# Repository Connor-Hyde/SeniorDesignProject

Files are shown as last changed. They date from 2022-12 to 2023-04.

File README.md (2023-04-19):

# Terra Table
# Table of Contents

1. [Project Description](#project-description)
2. [User Interface Specification](#user-interface-specification)
3. [Test Plan and Results](#test-plan-and-results)
4. [User Manual](#user-manual)
5. [Spring Final PPT Presentation](#spring-final-ppt-presentation)
6. [Final Expo Poster](#final-expo-poster)
7. [Assessments](#assessments)
    1. [Initial Self-Assessments](#initial-self-assessments)
    2. [Final Self-Assessments](#final-self-assessments)
8. [Summary of Hours and Justification](#summary-of-hours-and-justification)
9. [Summary of Expenses](#summary-of-expenses)
10. [Appendix](#appendix)

## Project Description

### Background
The purpose of this project is to elevate the gameplay experience of table-top role-playing games such as “Dungeons and Dragons”. These games are often played in the ‘theater of the mind’ using minimal props for visualizing the world in which the players are role-playing. However, many players do like to use a ‘battle mat’ to help visualize the specific locations and layouts of a certain area in the game.

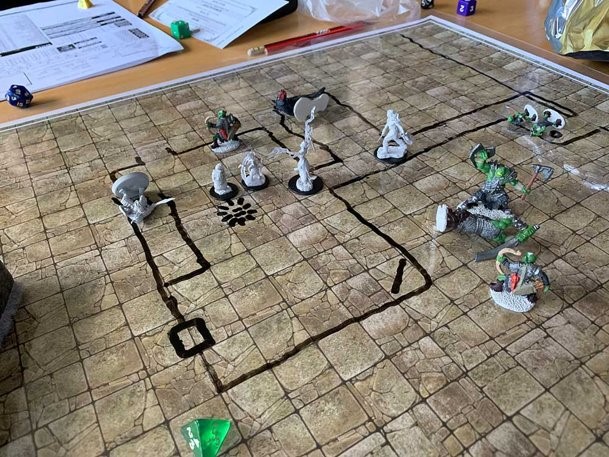
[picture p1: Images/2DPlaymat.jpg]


These mats consist of a large grid of squares. Each square represents a scaled down distance in game; players can use miniature figures of their characters to represent where they are in the world. The downside to these mats is that they are low tech and only two dimensional. Some players turn to using small blocks or walls to create a more 3D feeling to their environments, while others invest time and money into creating elaborate dioramas for their games.

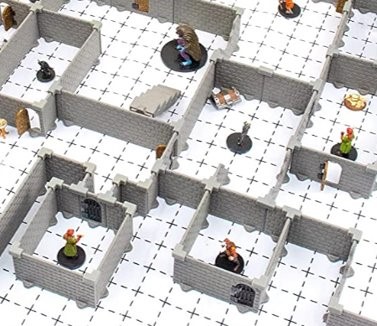
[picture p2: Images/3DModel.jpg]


This project aims to bridge the gap between low tech battle mats and high detail dioramas with programable, 3D topography, built into the game table.

### Objectives
This project aims to create a device that can be inserted into any table and convert it into a 3D topographical map that is fully programable to create scenes and landscapes for their gameplay. The final product will consist of a grid of cubes, each capable of being raised and lowered to create a 3D landscape. The shape of the scene will be determined by a graphical user interface where the players can create their map in 2D in the program and then watch as their creation comes to life in the table.

## User Interface Specification

The user interface was designed using Windows Presentation Foundation (WPF), and consists of 3 key features:

1. A slider for specifying height
2. 3 buttons, for executing actions
3. A 10x10 grid of squares, visually representing what the physical table will look like

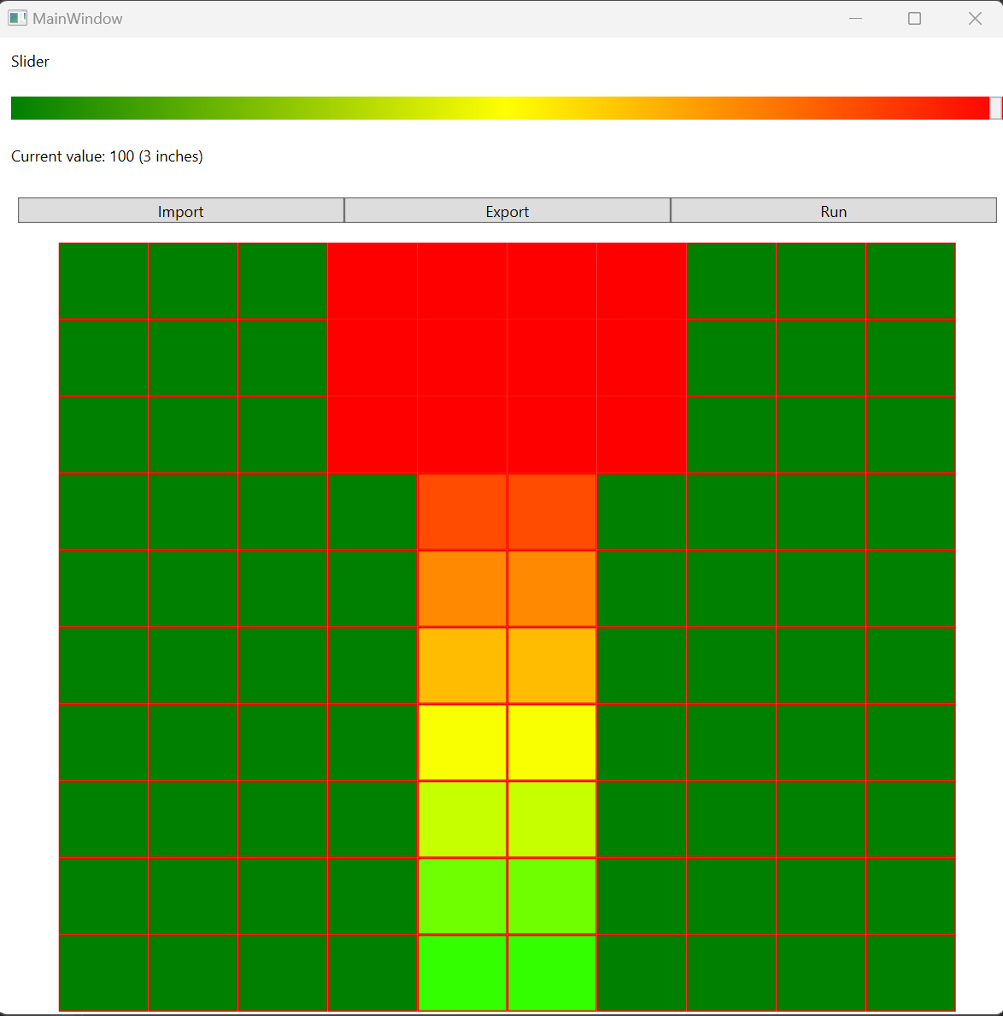
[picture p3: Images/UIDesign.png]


### Slider
The slider uses a gradient of colors from green to yellow to red, with a text box displaying the percentage of max height, and the corresponding height in inches. Whatever value is chosen on the slider will be applied to a grid square on click.

### Buttons
There are presently 3 buttons that allow the user to execute their respective actions:

1. Import: A text file can be imported, which will instantly apply a pre-recorded configuration to the grid.
2. Export: This exports the current configuration, so that at a later time it can be re-applied if desired.
3. Run: This executes the main functions of the table, sending the current configuration to the Arduino sketch. This is done by serialized communication with the board, and upon selecting this command the user will begin to see movements in the table until all cubes have been raised to desired height.

### Grid
The grid uses a gradient color scale to help the user visualize what they are creating on the table in 3 dimensions. From the image above, this would create something similar to a staircase, with a platform at the top. The idea was derived from topographical terrain maps that use gradients to visualize elevation on a 2 dimensional plane.

## Test Plan and Results

### Test Plan

For this project, the primary testing approach will be unit testing, supplemented by integration testing for more complex components. The goal is to adhere to Test-Driven Development (TDD) practices as closely as possible, as this has become a habit in professional work environments. Although TDD can sometimes be tedious, it is crucial to ensure that methods and classes are thoroughly tested.

Regardless of the specific approach, the project will have as many components (methods and classes) tested as feasible. Integration tests may be required when developing the Arduino aspect of the project, which might necessitate exploring various test suites capable of running both code segments concurrently in a single test.

For unit testing, NCrunch, a valuable tool for debugging and viewing all tests within a given solution simultaneously, will be utilized. Mocking frameworks and NUnit will be employed to construct the tests.

### Test Results

All tests can be found in the /Code/TerrainTableWpf/Tests subdirectory. There were 10 tests in total to ensure that all logic is set up properly, the testing matrix summarizing all aspects of the testing can be found below:

| Test Identifier | Purpose of Test | Inputs for Test | Expected Outputs/Results | Unit Test Indication |
| --- | --- | --- | --- | --- |
| MainWindowConstructor_CreatesExpectedTerrainGrid | Tests that the construction of the UI grid sets the initial state properly | None | Expected that all squares have an initial 'Green' state | Pass |
| ReadFileContent_ReturnsCorrectFileContent | Ensures the file reader returns exactly what is in the text files for importing | Encoded string of file content | Should return string decoded | Pass |
| DeserializeAndSetTerrainGrid_SetsTerrainGridHeightsCorrectly | Verifies that an array passed in sets the UI grid heights properly | String array representing square heights | Should set height of each terrain square | Pass
| SendSerializedGridToSerialPort_WritesSerializedGridToSerialPort | Verifies that the grid is sent to serial port of Arduino board | Serialized grid and port wrapper object | Should call port.write() with serialized grid as parameter | Pass
| SerializeGrid_SameHeightValues_ReturnsSerializedGrid | Sets the grid heights and checks that serialize grid returns the proper string | None | Should set serialized grid to same value as expected | Pass
| SerializeGrid_DifferentHeightValues_ReturnsSerializedGrid | Same test as previous, this time giving each square different heights | None | Should set serialized grid to same value as expected | Pass
| IntToColor_ValueZero_SetsGreenColor | Verifies that when 0 is passed in the color green is set | Integer height | Specified color set on main window green | Pass
| IntToColor_ValueOneHundred_SetsRedColor | Verifies that when 100 is passed in the color red is set | Integer height | Specified color set on main window red | Pass
| IntToColor_ValueFifty_SetsYellowColor | Verifies that when 50 is passed in the color yellow is set | Integer height | Specified color set on main window yellow | Pass
| Slider2_ValueChanged_ValueChanged_SetsSliderValueAndTextBlock1Text | Asserts that changing the slider position updates both the value and inches field | Property changed arguments | Percentage height and inches | Pass

## User Manual

[View the user manual directly here.](Assignments/TerraTableUserManual.pdf)
The user manual for this project was created to be printable, so was put in PDF form. Ideally, it would be shipped with the table all in one package.

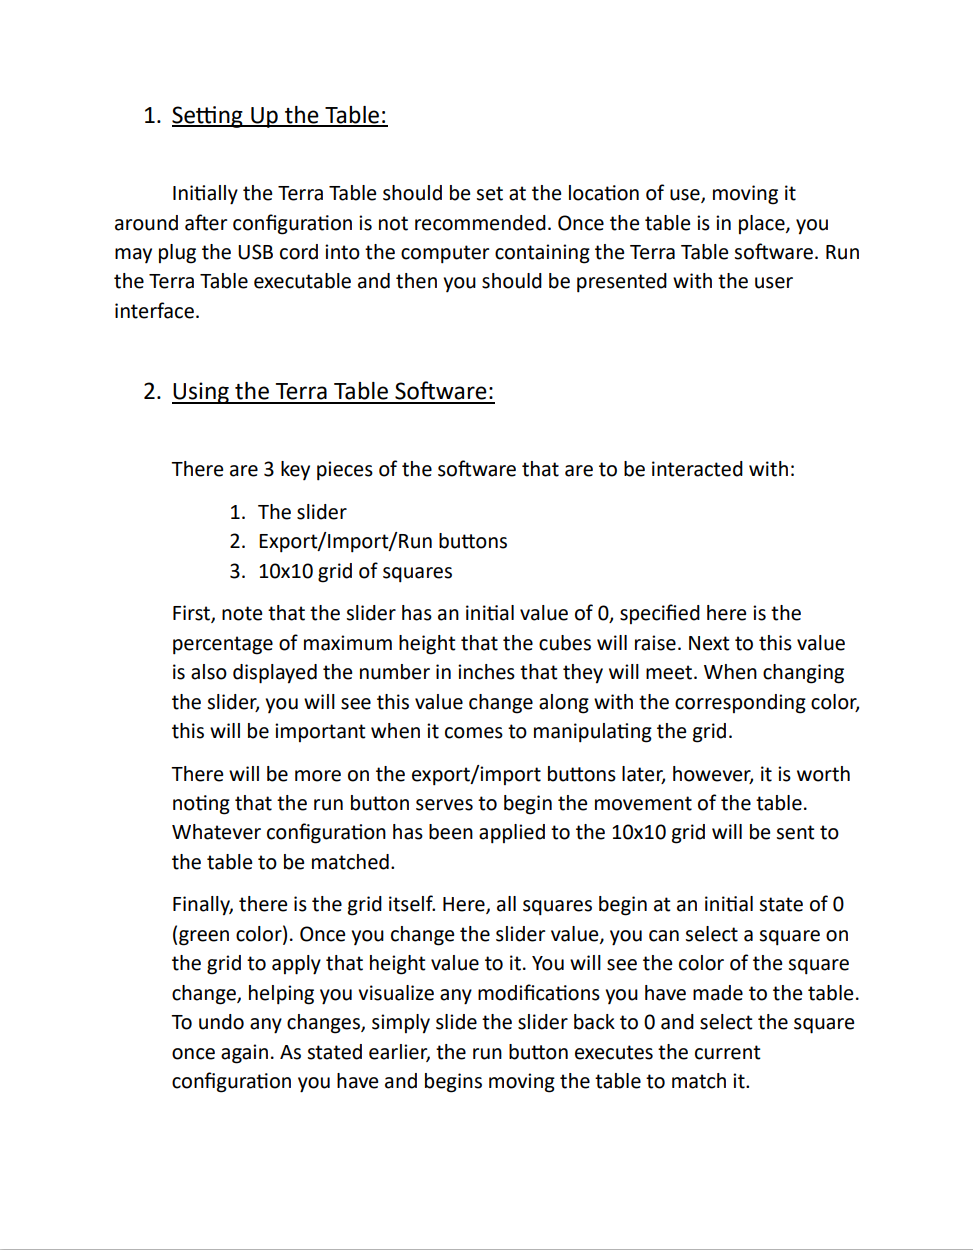
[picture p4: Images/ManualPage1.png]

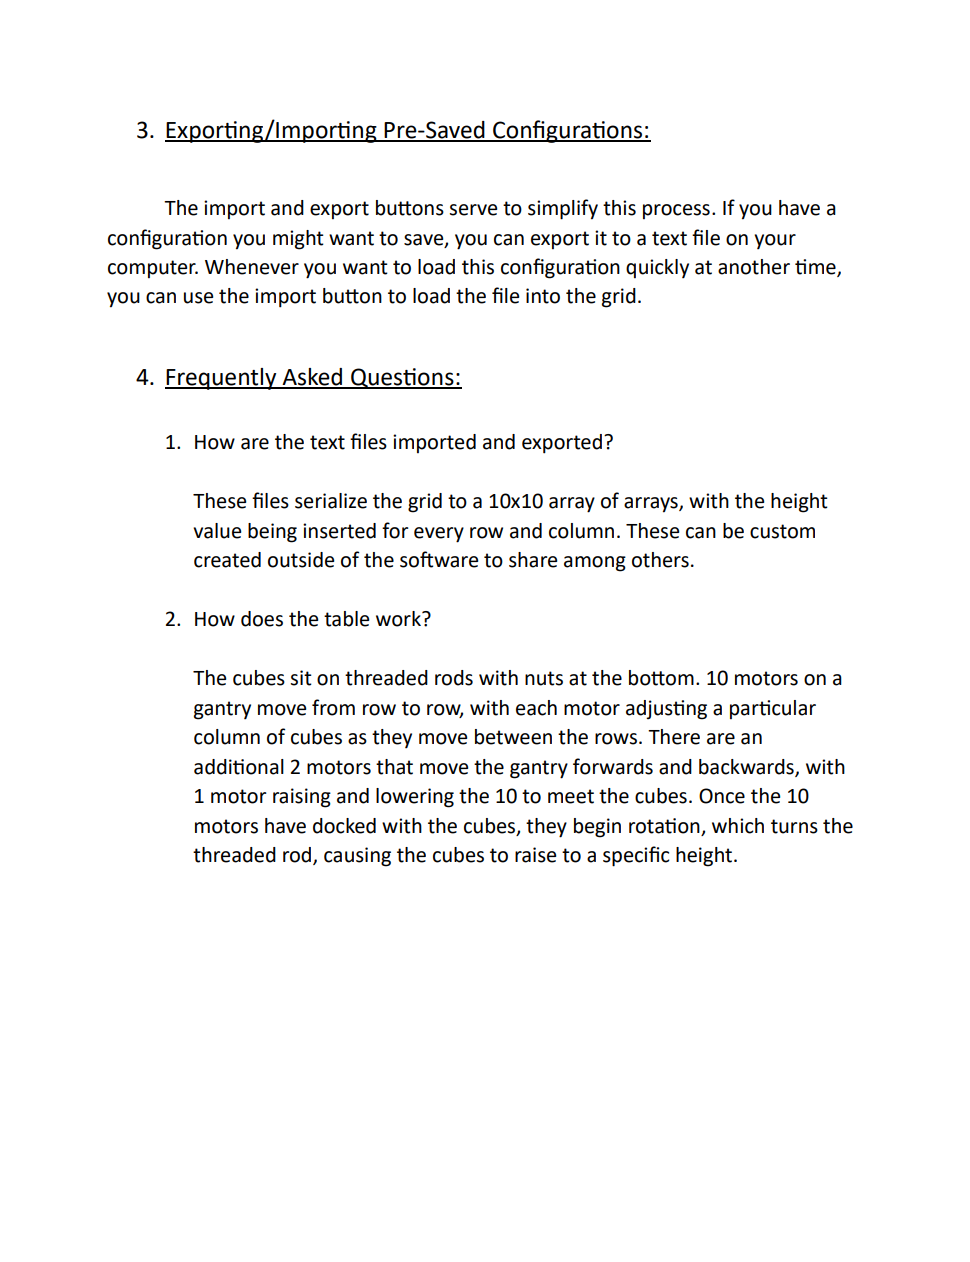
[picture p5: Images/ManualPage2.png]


## Spring Final PPT Presentation

[View the final presentation here.](Assignments/FinalPresentation.pptx)

## Final Expo Poster

[View the expo presentation here.](Assignments/ExpoPresentation.pptx)

## Assessments

### Initial Self-Assessments

Having developed a preliminary outline of the table's functionality and codebase, I have identified potential challenges and viable solutions. The most significant challenge involves writing the Arduino code, as this will be my first foray into programming a physical device, a departure from my prior experience in digital programming. Additionally, our team lacks electrical or computer engineering expertise, which may complicate the wiring and circuitry aspects of the project.

Regarding the user interface, I possess prior experience with Windows Presentation Foundation (WPF), which should facilitate a relatively seamless execution of this project component. Although my expertise in XAML is limited, my understanding of the fundamentals should be sufficient to prevent major obstacles during the project. I anticipate that designing and testing the user interface will consume less time than integrating the various components.

The primary focus of our efforts will likely be perfecting the motor movements and establishing the table's circuitry, which will prove essential to the successful completion of the project.

### Final Self-Assessments

My most significant contribution to the project was undoubtedly the codebase, encompassing both the Arduino and User Interface (UI) elements. Collaborating with two Mechanical Engineers, I was aware from the outset that the responsibility for all coding tasks would fall to me. During the planning phase, I identified challenges and knowledge gaps that could hinder progress. However, I am pleased to report that these obstacles were successfully overcome.

Developing the codebase entailed two primary components: the UI and the Arduino code. The UI was designed using Windows Presentation Foundation (WPF) and involved creating an MVVM (Model-View-ViewModel) application to enable user interaction. Although the program operates as intended, I encountered difficulties in adhering to the MVVM principles. The majority of my logic is housed in the MainWindow file, which is less than ideal within this architectural framework.

Despite these challenges, I gained valuable experience working with XAML and Arduino, and I now feel more confident in writing code using these languages. My personal greatest obstacle was serializing data from the UI to the Arduino board. Given my limited knowledge of circuitry, even seemingly minor tasks involving physical interaction with the code proved difficult to overcome.

## Summary of Hours and Justification

| Name | Semester 1 Hours | Semester 2 Hours | Year Hours |
|---|---|---|---|
| Luke | 24 | 48 | 72 |
| Quinton | 24 | 48 | 72 |
| Connor  | 24 | 48 | 72 |

Total hours: 216

We each only met when all were available, with the first semester consisting of 6 meetings regarding planning. In these meetings, Connor drafted flowcharts and researched architectures for the codebase, while Quinton and Luke created CAD drawings and modeled the product.

Semester 2 had 6 meetings in which we coded/assembled the table, which were each 4 hours each. As the expo approached, we had 3 8 hour days devoted to finishing up the table. This was almost all devoted to soldering capacitors, setting up the circuits, debugging the motors, and finishing assembly. In the appendix below you will find links to CAD drawings, diagrams, and pictures of the product that we took along the way.

Additionally, there were four phases compiled and formatted into a Gantt chart to keep track of tasks.

### Phase 1

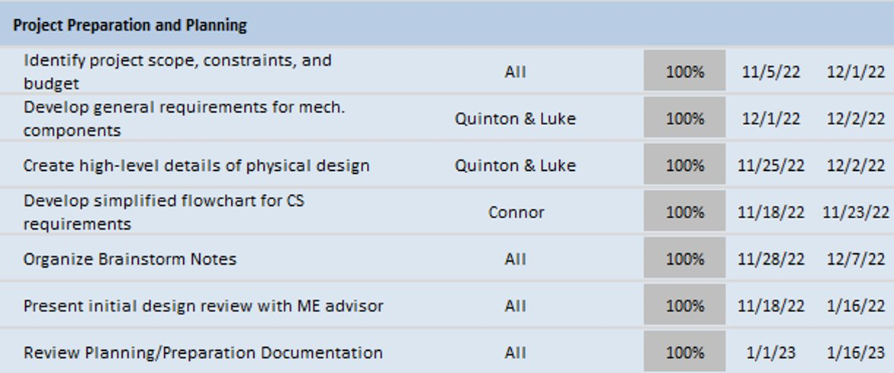
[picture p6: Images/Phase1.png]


### Phase 2

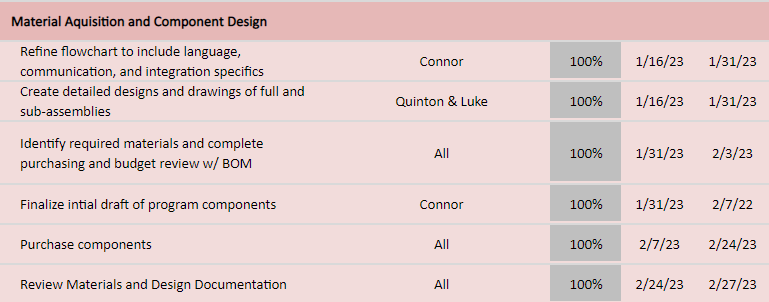
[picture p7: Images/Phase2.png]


### Phase 3

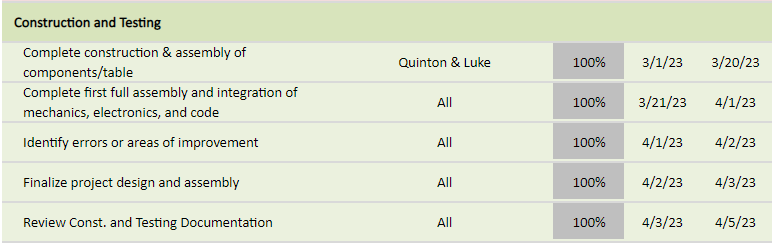
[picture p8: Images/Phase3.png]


### Phase 4

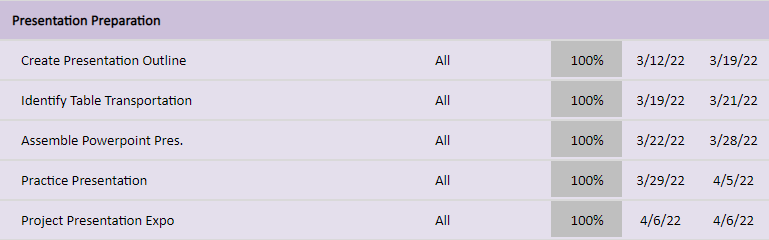
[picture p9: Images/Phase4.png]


## Summary of Expenses

We were able to organize our entire bill of materials into a concise table:
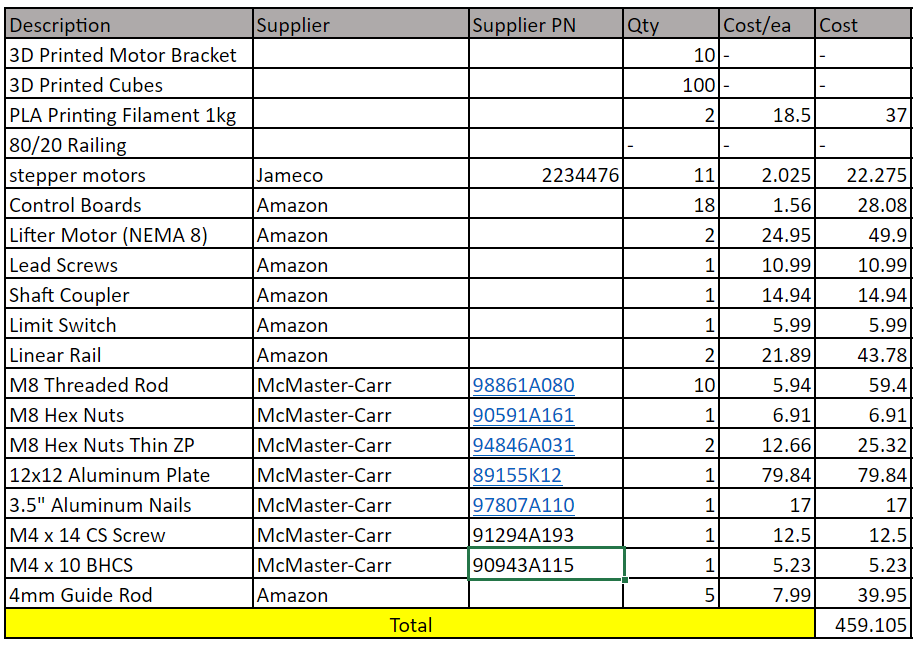
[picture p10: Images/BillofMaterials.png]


## Appendix

### Drawings and Diagrams

[Motor calculations and rough drawings of design.](Notes/MotorsRoughDraft.pdf)

[Fully rendered model of the full assy.](Images/TableModelRendered.jpg)

[Detailed model of motor/cube relationship and setup.](Images/MotorsAndCubes.jpg)

[Cross section of the cubes visualizing the inserted threaded rod.](Images/CubeCrossSection.jpg)

### References

US bolts - tightening torques. Engineering ToolBox. (n.d.). Retrieved February 24, 2023, from https://www.engineeringtoolbox.com/us-bolts-torques-d_2055.html 

Beams - supported at both ends - continuous and point loads. Engineering ToolBox. (n.d.). Retrieved February 24, 2023, from https://www.engineeringtoolbox.com/beam-stress-deflection-d_1312.html 

Electric Motor Calculator. Engineering ToolBox. (n.d.). Retrieved February 24, 2023, from https://www.engineeringtoolbox.com/electrical-motor-calculator-d_832.html 

ASTM F963-17: Standard Consumer Safety Specification for Toy Safety, ASTM International Retrieved February 24, 2023,  
The Federal Register. Federal Register :: Request Access. (n.d.). Retrieved February 24, 2023, from https://www.ecfr.gov/current/title-16 

ULN2003 stepper motor drivers - electronicos caldas. (n.d.). Retrieved February 25, 2023, from https://www.electronicoscaldas.com/datasheet/ULN2003A-PCB.pdf 

Wilson, A. (2009, June 4). WPF colour slider. CodeProject. Retrieved February 24, 2023, from https://www.codeproject.com/Articles/36802/WPF-Colour-Slider

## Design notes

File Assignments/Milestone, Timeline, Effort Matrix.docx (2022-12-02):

Milestones:

Project Planning: Outline all tasks needed to be completed for the project

Research: Figure out which components will need to be purchased for table, which programming language to use for code

Development: Create program and build table

Testing: Stress test both the code and table itself

Refinement: Iron out any issues remaining after testing

Presentation: Assemble project documents for presentations and report

Timeline:

TASK | ASSIGNED TO | PROGRESS | START | END
Project Preparation and Planning
Identify project scope, constraints, and budget | All | 100% | 12/1/22 | 11/25/22
Develop general requirements for mech. components | Quinton & Luke | 0% | 11/25/22 | 12/2/22
Create high-level details of physical design | Quinton & Luke | 0% | 11/25/22 | 12/2/22
Develop simplified flowchart for CS requirements | Connor | 63% | 11/18/22 | 11/23/22
Organize Brainstorm Notes | All | 0% | 11/28/22 | 12/7/22
Present initial design review with ME advisor | All | 0% | 11/18/22 | 1/16/22
Review Planning/Preparation Documentation | All | 0% | 1/1/22 | 1/16/22
Material Aquisition and Component Design
Refine flowchart to include language, communication, and integration specifics | Connor | 0% | 1/16/22 | 1/31/22
Create detailed designs and drawings of full and sub-assemblies | Quinton & Luke | 0% | 1/16/22 | 1/31/22
Identify required materials and complete purchasing and budget review w/ BOM | All | 0% | 1/31/22 | 2/3/22
Finalize initial draft of program components | Connor | 0% | 1/31/22 | 2/7/22
Purchase components | All | 0% | 1/31/22 | 2/3/22
Review Materials and Design Documentation | All | 0% | 1/31/22 | 2/3/22
Construction and Testing
Complete construction & assembly of components/table | Quinton & Luke | 0% | 2/1/22 | 3/9/22
Complete first full assembly and integration of mechanics, electronics, and code | All | 0% | 3/10/22 | 3/12/22
Identify errors or areas of improvement | All | 0% | 3/12/22 | 3/14/22
Finalize project design and assembly | All | 0% | 3/13/22 | 3/17/22
Review Const. and Testing Documentation | All | 0% | 3/15/22 | 3/19/22
Presentation Preparation
Create Presentation Outline | All | 0% | 3/12/22 | 3/19/22
Identify Table Transportation | All | 0% | 3/19/22 | 3/21/22
Assemble PowerPoint Pres. | All | 0% | 3/22/22 | 3/28/22
Practice Presentation | All | 0% | 3/29/22 | 4/5/22
Project Presentation Expo | All | 0% | 4/6/22 | 4/6/22

Effort Matrix:

Task | Effort
Identify project scope, constraints, and budget | Quinton 33%, Luke 33%, Connor 33%
Develop general requirements for mech. components | Quinton 50%, Luke 50%
Create high-level details of physical design | Quinton 50%, Luke 50%
Develop simplified flowchart for project CS requirements | Connor 100%
Present initial design review with ME advisor | Quinton 33%, Luke 33%, Connor 33%
Refine flowchart to include language, communication, and integration specifics | Connor 100%
Create detailed designs and drawings of full and sub-assemblies | Quinton 50%, Luke 50%
Identify required materials and complete purchasing and budget review | Quinton 33%, Luke 33%, Connor 33%
Begin construction of assembly of components/table | Quinton 33%, Luke 33%, Connor 33%
Finalize initial draft of program components | Connor 100%
Complete first full assembly and integration of mechanics, electronics, and code | Quinton 33%, Luke 33%, Connor 33%
Identify errors or areas of improvement | Quinton 33%, Luke 33%, Connor 33%
Finalize project design and assembly | Quinton 33%, Luke 33%, Connor 33%
Prepare presentation materials for final review | Quinton 33%, Luke 33%, Connor 33%

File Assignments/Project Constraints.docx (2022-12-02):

Economic

One of the first things our group considered when we initially had this project idea was whether it was feasible for us to do simply out of cost. Depending on how the table is set up, whether we have too large a table, or too many motors, we could easily skyrocket the cost of this project into something we can’t afford. Cost will play a major role as we continue with developing this project.

Target Audience

As we are building something to be used for hobbies, the target audience is already going to be narrowed significantly. On top of this, we also need to manage the economic constraint or that target audience would shrink even further to only those that could afford such a product.

Technical Knowledge

For Connor, working with Arduino is something new and developing code that will bring something in the real world to life is something he’s never done before. It will be a great learning experience and will push his knowledge of Arduino/machine language. For Quinton and Luke, they will be putting their learning to the test when it comes to building a system of motors and making it all work properly.

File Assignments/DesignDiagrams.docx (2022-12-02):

User Stories

1. As a player, I want a mechanical table that displays topography in 3-D for tabletop role playing games like Dungeons & Dragons.
2. As a game master, I want to design and upload different terrains or geographical features for the topographical table to generate and display in 3-dimensions.
3. As a user, I want an on-board interface with preset layouts that can be selected from a digital menu.
4. As a game master, I want a desktop interface to control individual modules.
5. As a player, I want the table to adjust to new environments in a minimal amount of time (<2min).

Design Diagrams:

The diamonds represent program specific steps, while the squares represent mechanical steps.

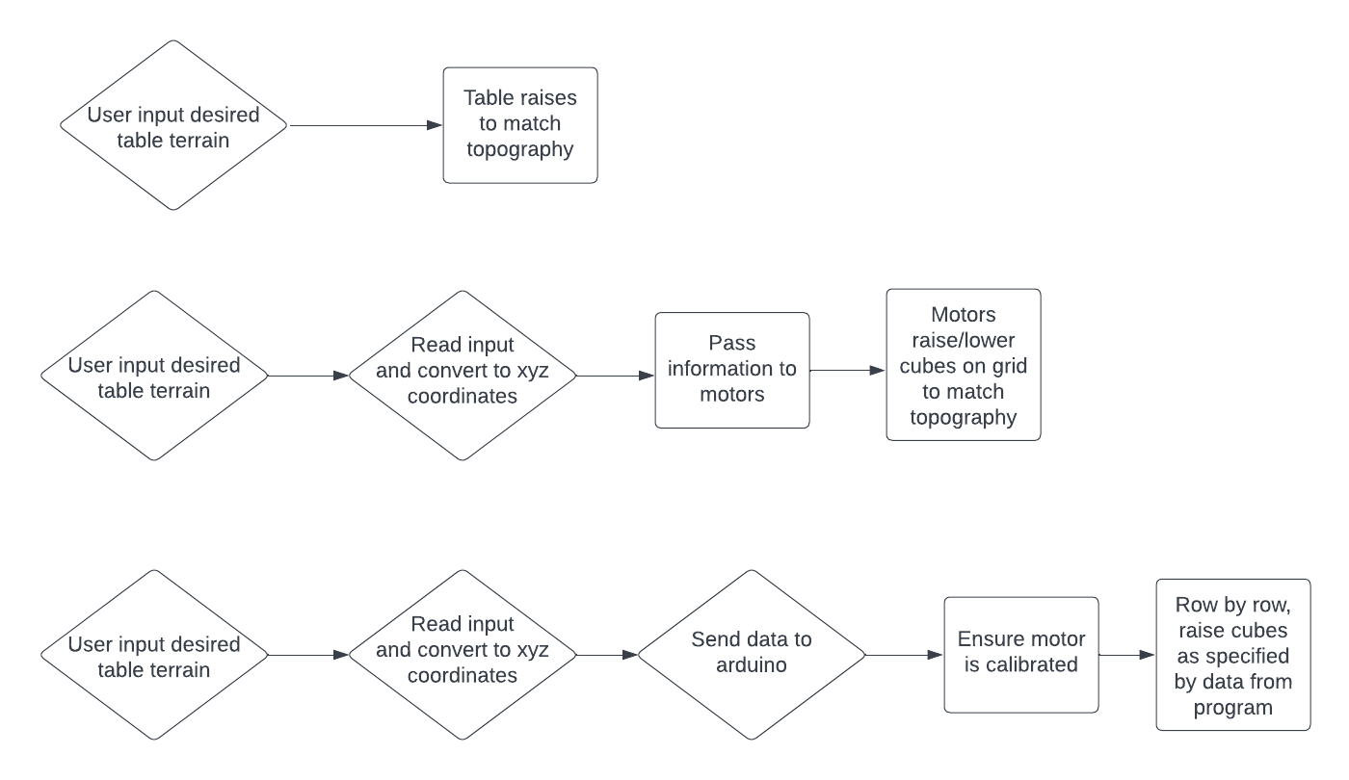
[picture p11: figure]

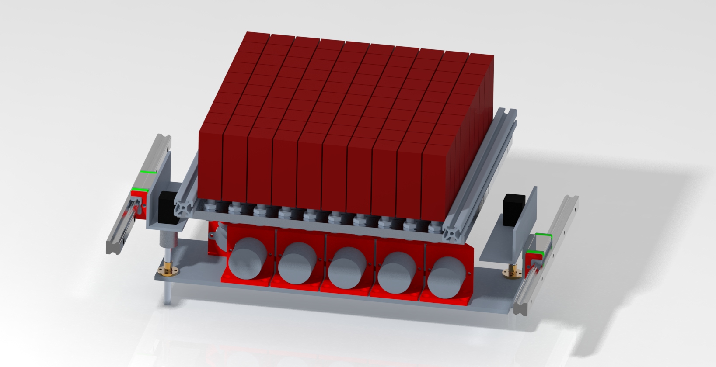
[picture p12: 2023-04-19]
Images/TableModelRendered.jpg

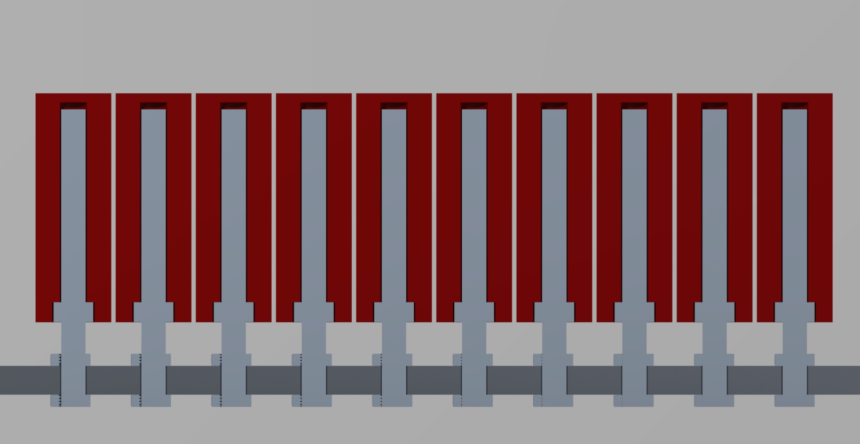
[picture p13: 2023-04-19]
Images/CubesCrossSection.jpg

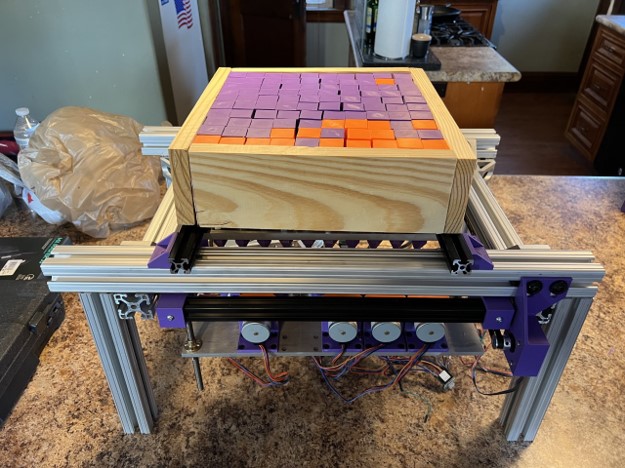
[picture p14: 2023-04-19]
Images/TerraTable.jpg

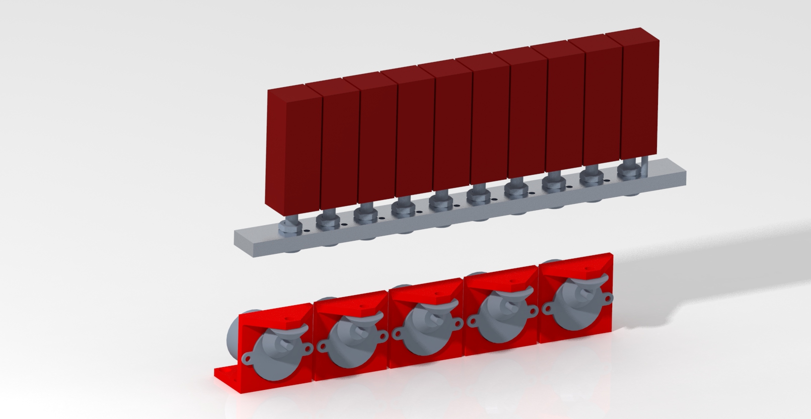
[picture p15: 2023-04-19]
Images/MotorsAndCubes.jpg

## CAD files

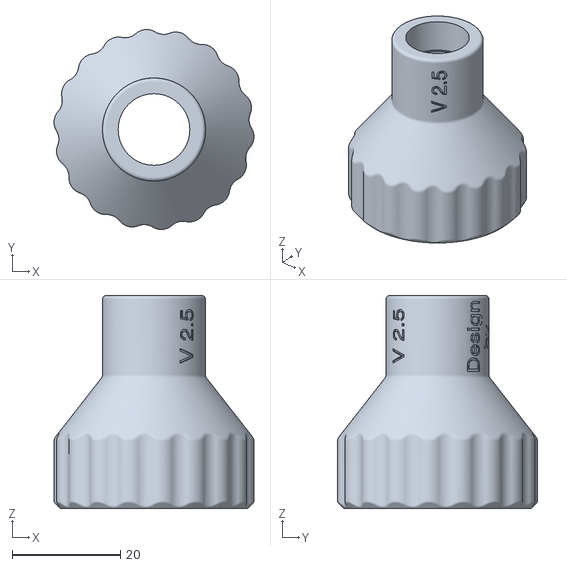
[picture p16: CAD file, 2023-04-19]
3DFiles/nozzle_torque_wrench_housing.stl
36.9 x 36.9 x 39.3

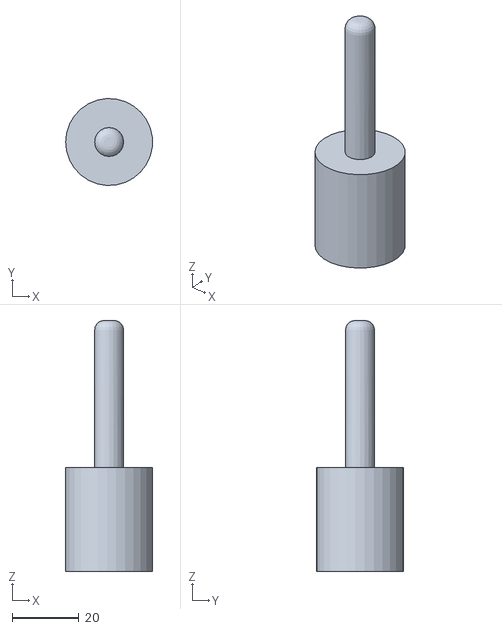
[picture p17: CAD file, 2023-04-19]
3DFiles/Solder/Probe2.stl
25.9 x 26.0 x 75.0

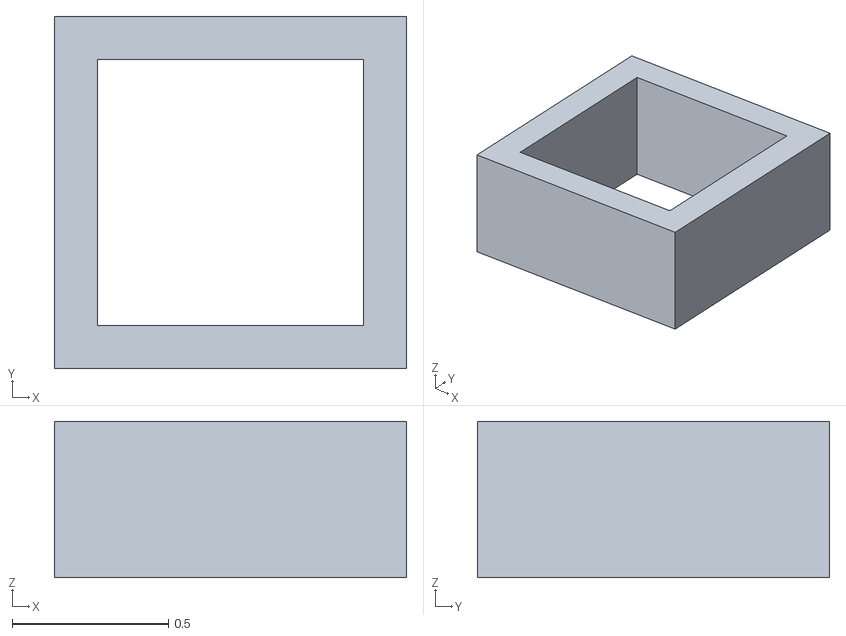
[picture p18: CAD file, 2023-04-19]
3DFiles/STL/2020testfit.stl
1.12 x 1.12 x 0.5

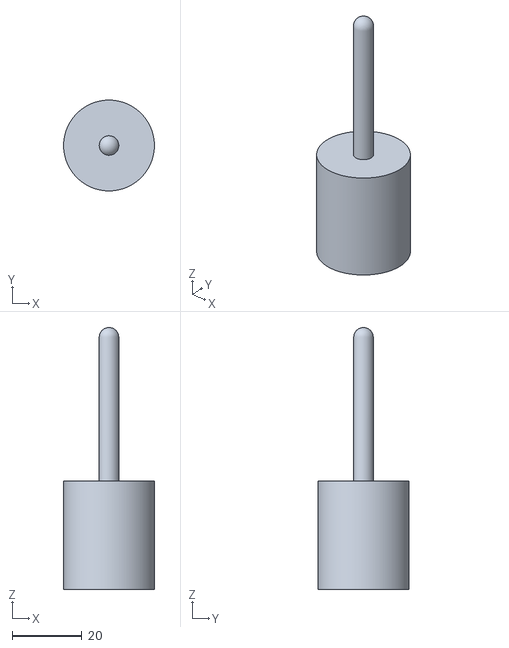
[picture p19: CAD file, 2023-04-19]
3DFiles/Solder/Probe.stl
26.0 x 26.0 x 75.0

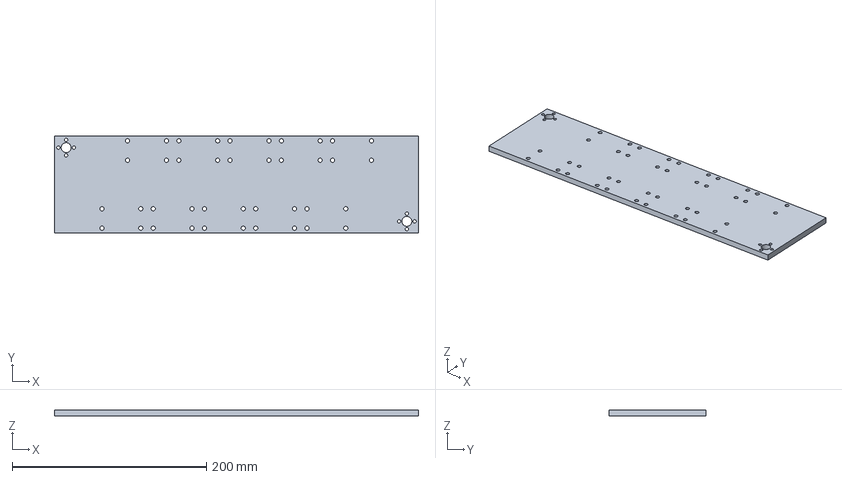
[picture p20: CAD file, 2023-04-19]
3DFiles/STL/gantryplate.stp
375.0 x 100.0 x 6.35 mm

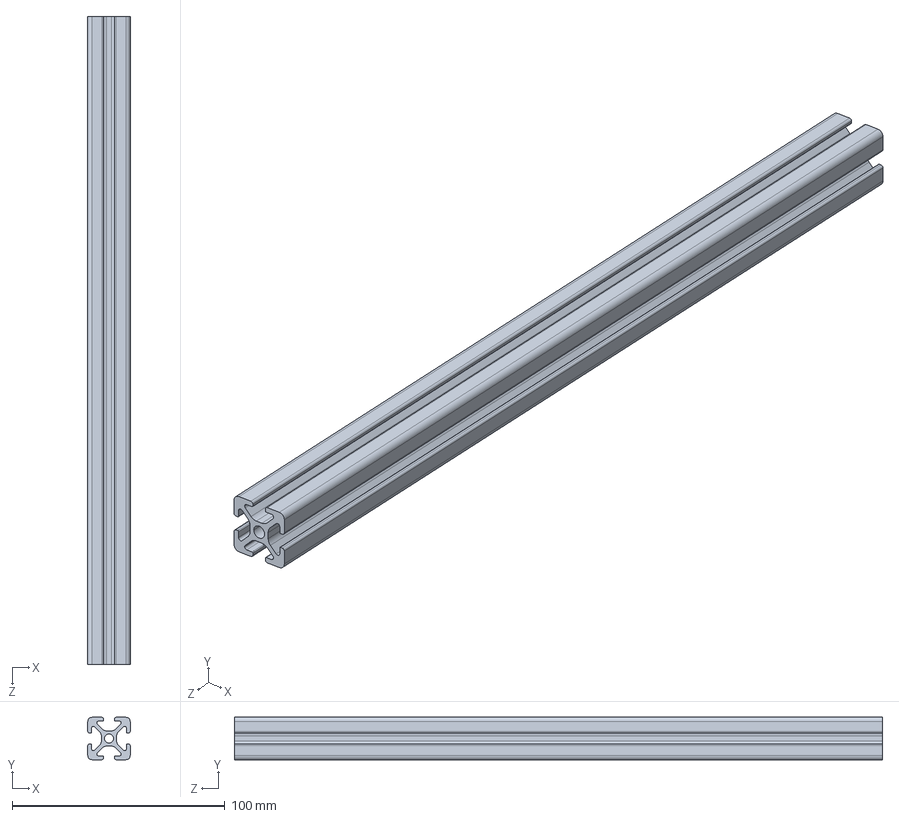
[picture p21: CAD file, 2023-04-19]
3DFiles/5537T9_T-Slotted Framing.STEP
20.0 x 20.0 x 304.8 mm

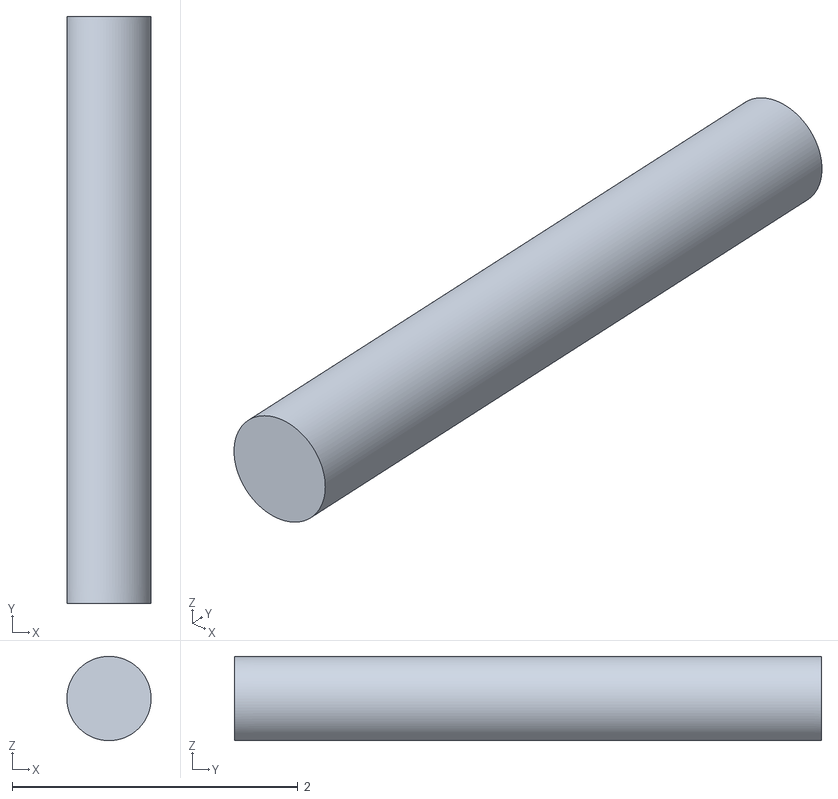
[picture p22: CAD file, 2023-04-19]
3DFiles/STL/cuttingjig.stl
0.59 x 4.11 x 0.59

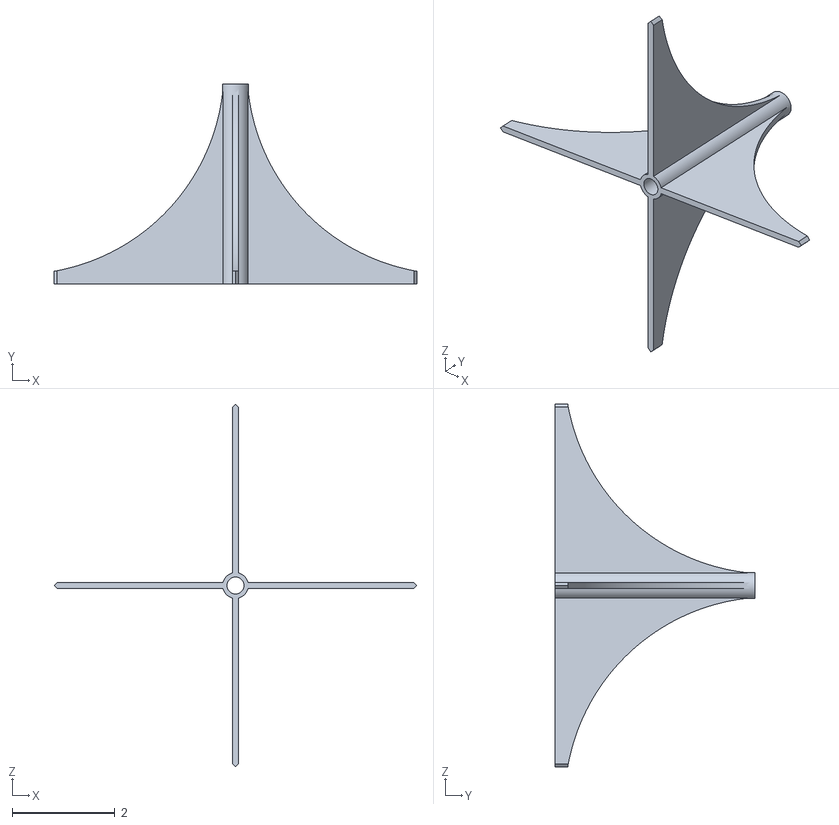
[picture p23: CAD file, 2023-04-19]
3DFiles/STL/jigsolderrev2.stl
7.07 x 3.90 x 7.07

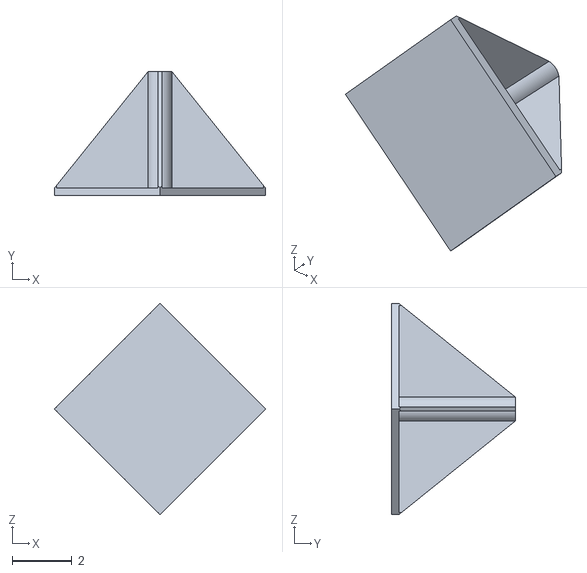
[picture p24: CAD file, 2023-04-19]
3DFiles/STL/jigsolder.stl
7.07 x 4.15 x 7.07

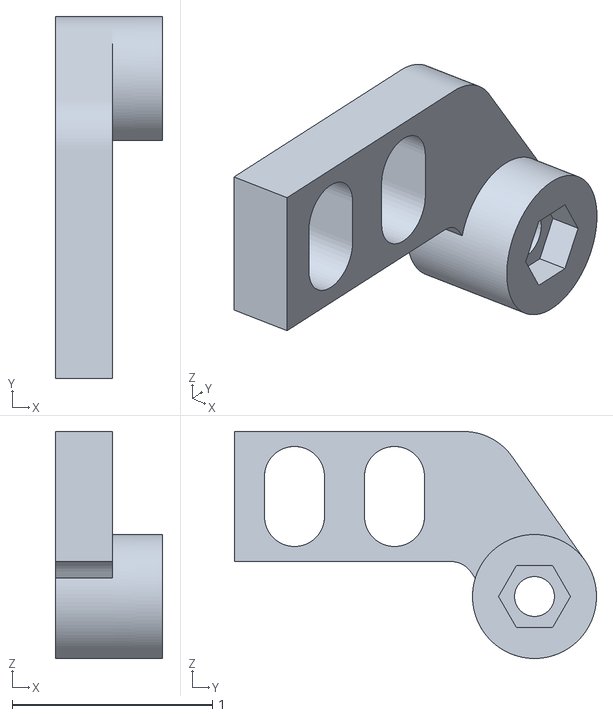
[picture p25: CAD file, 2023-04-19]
3DFiles/STL/idlewheelbracket.stl
0.535 x 1.81 x 1.13

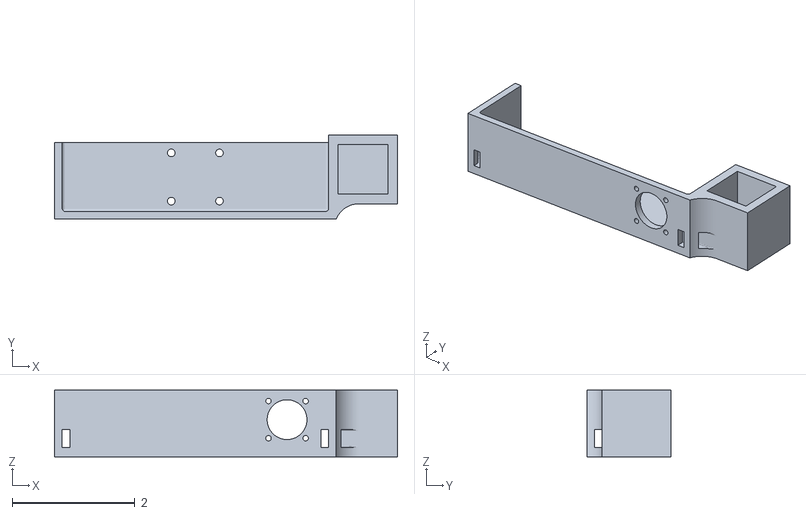
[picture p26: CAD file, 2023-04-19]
3DFiles/STL/linearrailbracketrev2mirror.stl
5.60 x 1.38 x 1.09

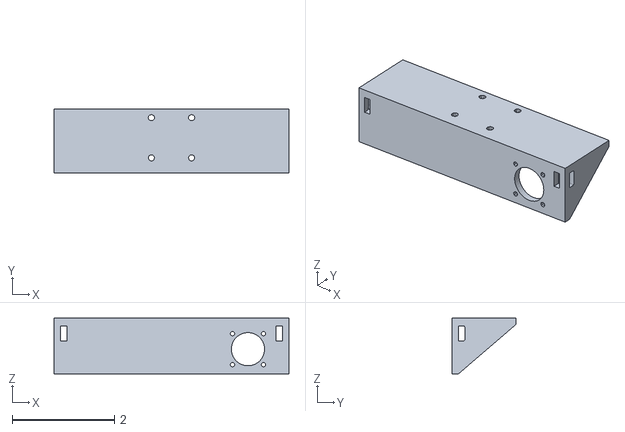
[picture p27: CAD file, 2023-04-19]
3DFiles/STL/linearrailbracket.stl
4.60 x 1.25 x 1.09

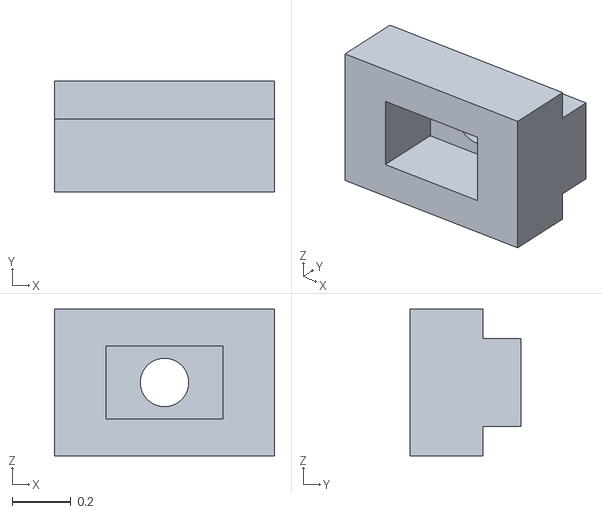
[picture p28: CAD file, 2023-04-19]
3DFiles/STL/m4tnutadapter.stl
0.75 x 0.38 x 0.5

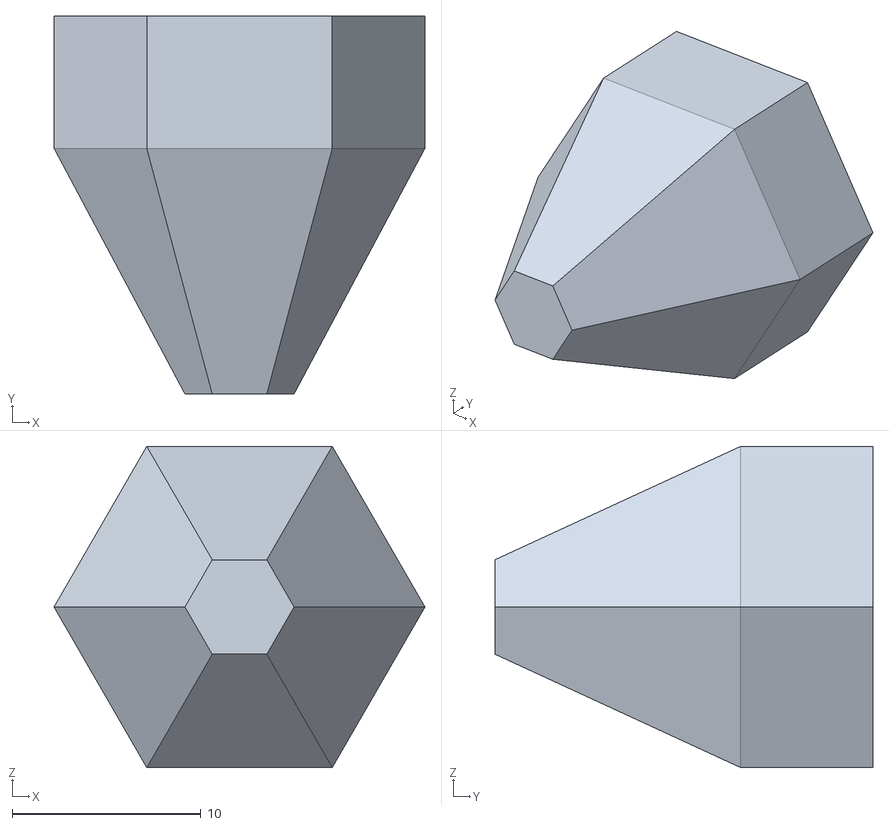
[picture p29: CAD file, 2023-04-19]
3DFiles/STL/leadinnut.stl
19.6 x 20.0 x 17.0

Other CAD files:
3DFiles/STL/linearrailbracketrev2.stl
3DFiles/STL/gantrymotormount.stl
3DFiles/STL/cube_gantry.stp
3DFiles/STL/linearrailbracketrev2right.stl
3DFiles/47065T601_T-Slotted Framing.STEP
3DFiles/90326A105_Steel Thin Hex Nut.STEP
3DFiles/90592A022_Steel Hex Nut.STEP
3DFiles/97807A110_Aluminum Nails.STEP
3DFiles/STL/cornerbracketcubes.stl
3DFiles/STL/gearspacer.stl
3DFiles/Solder/Probe.prt
3DFiles/Solder/Probe2.prt
3DFiles/cube_gantry.dxf
3DFiles/gantryplate.dxf

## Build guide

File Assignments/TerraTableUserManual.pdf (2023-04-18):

# Terra Table User Manual

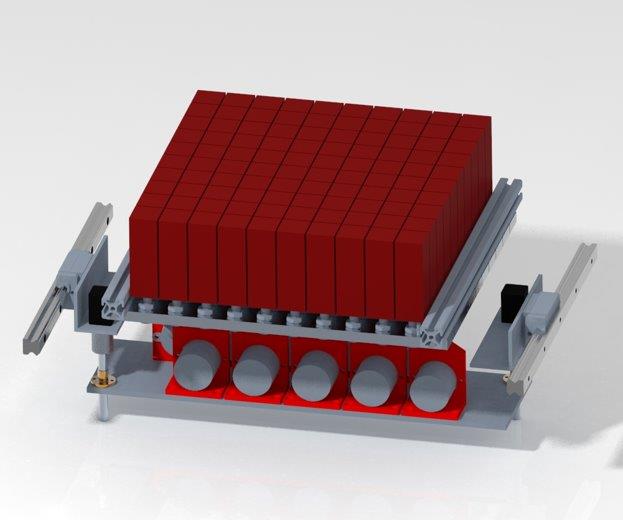
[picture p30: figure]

## Table of Contents

1. Setting Up the Table
2. Using the Terra Table Software
3. Exporting/Importing Pre-Saved Configurations
4. Frequently Asked Questions

1. Setting Up the Table:

Initially the Terra Table should be set at the location of use, moving it around after configuration is not recommended. Once the table is in place, you may plug the USB cord into the computer containing the Terra Table software. Run the Terra Table executable and then you should be presented with the user interface.

2. Using the Terra Table Software:

There are 3 key pieces of the software that are to be interacted with:

1. The slider
2. Export/Import/Run buttons
3. 10x10 grid of squares

First, note that the slider has an initial value of 0, specified here is the percentage of maximum height that the cubes will raise. Next to this value is also displayed the number in inches that they will meet. When changing the slider, you will see this value change along with the corresponding color, this will be important when it comes to manipulating the grid.

There will be more on the export/import buttons later, however, it is worth noting that the run button serves to begin the movement of the table. Whatever configuration has been applied to the 10x10 grid will be sent to the table to be matched.

Finally, there is the grid itself. Here, all squares begin at an initial state of 0 (green color). Once you change the slider value, you can select a square on the grid to apply that height value to it. You will see the color of the square change, helping you visualize any modifications you have made to the table. To undo any changes, simply slide the slider back to 0 and select the square once again. As stated earlier, the run button executes the current configuration you have and begins moving the table to match it.

3. Exporting/Importing Pre-Saved Configurations:

The import and export buttons serve to simplify this process. If you have a configuration you might want to save, you can export it to a text file on your computer. Whenever you want to load this configuration quickly at another time, you can use the import button to load the file into the grid.

4. Frequently Asked Questions:
1. How are the text files imported and exported?

These files serialize the grid to a 10x10 array of arrays, with the height value being inserted for every row and column. These can be custom created outside of the software to share among others.

2. How does the table work?

The cubes sit on threaded rods with nuts at the bottom. 10 motors on a gantry move from row to row, with each motor adjusting a particular column of cubes as they move between the rows. There are an additional 2 motors that move the gantry forwards and backwards, with 1 motor raising and lowering the 10 to meet the cubes. Once the 10 motors have docked with the cubes, they begin rotation, which turns the threaded rod, causing the cubes to raise to a specific height.

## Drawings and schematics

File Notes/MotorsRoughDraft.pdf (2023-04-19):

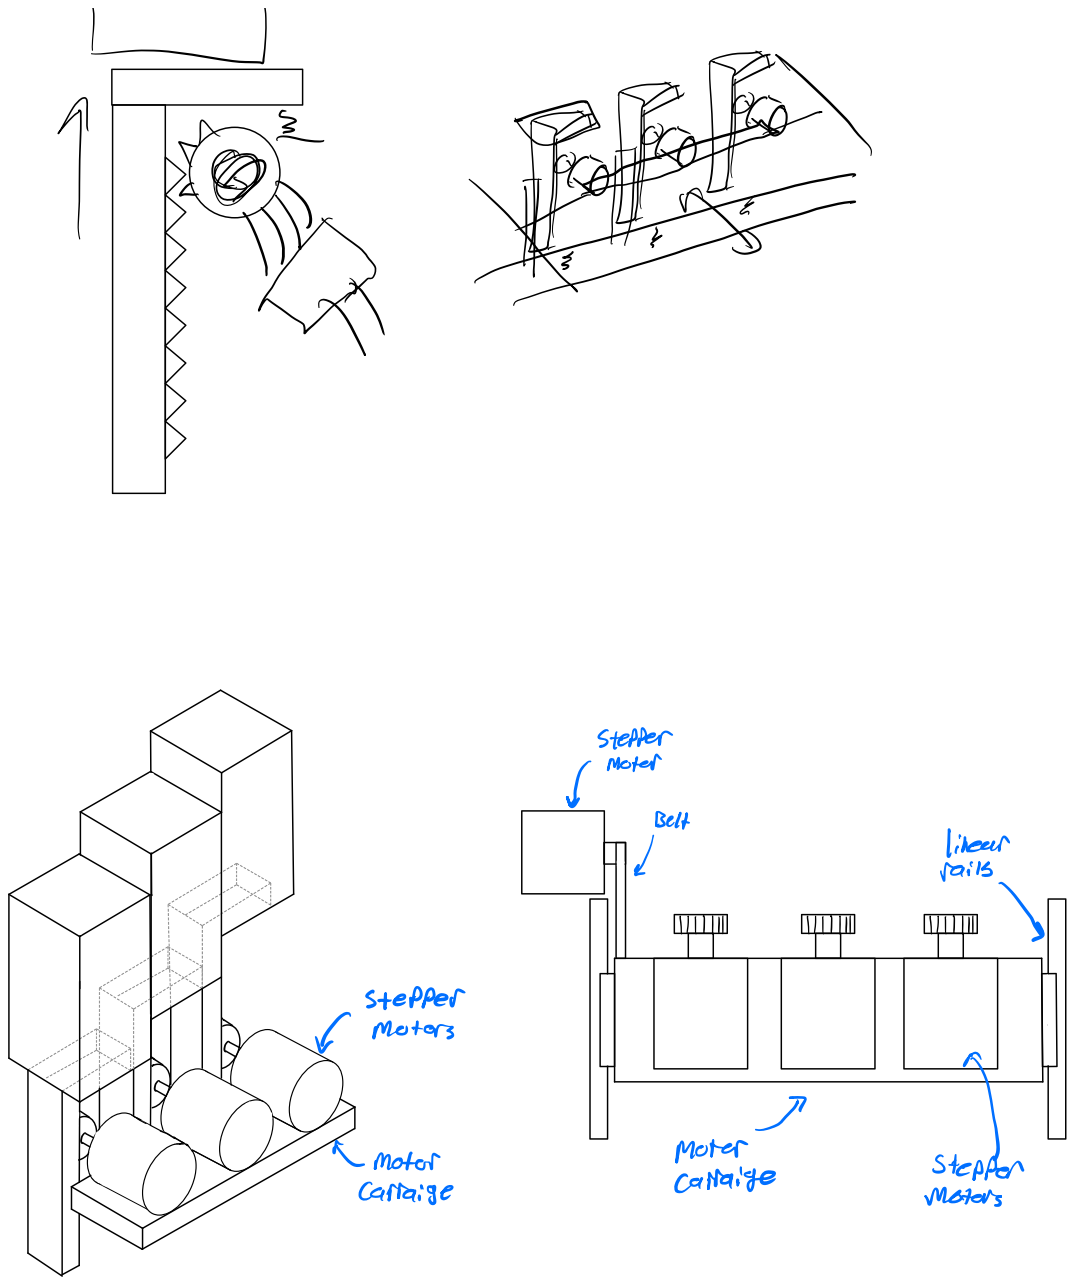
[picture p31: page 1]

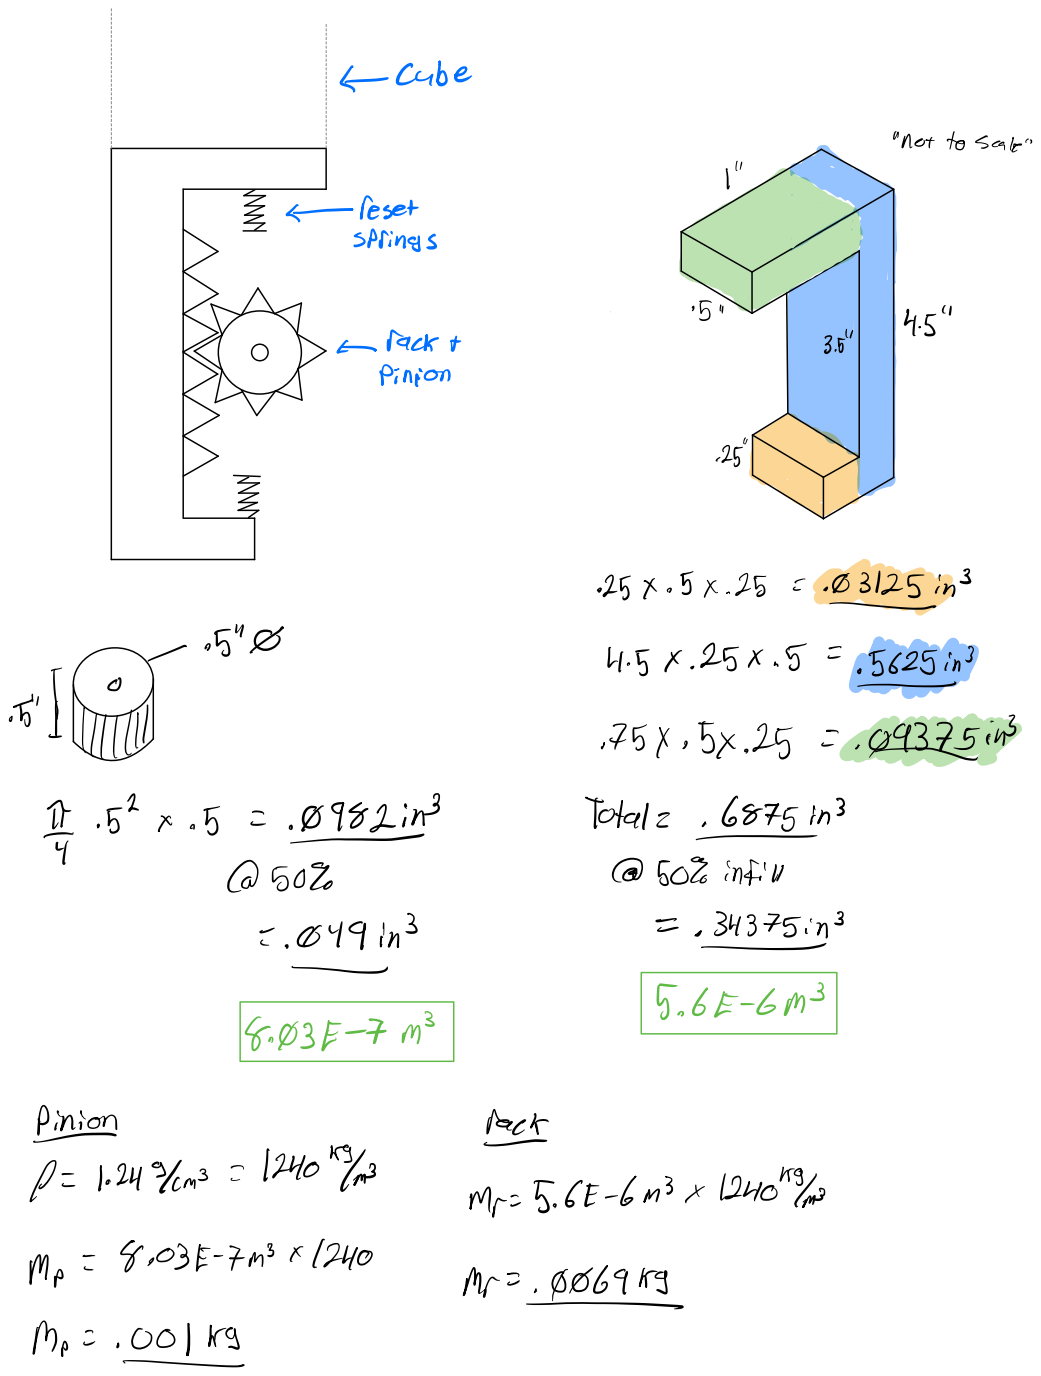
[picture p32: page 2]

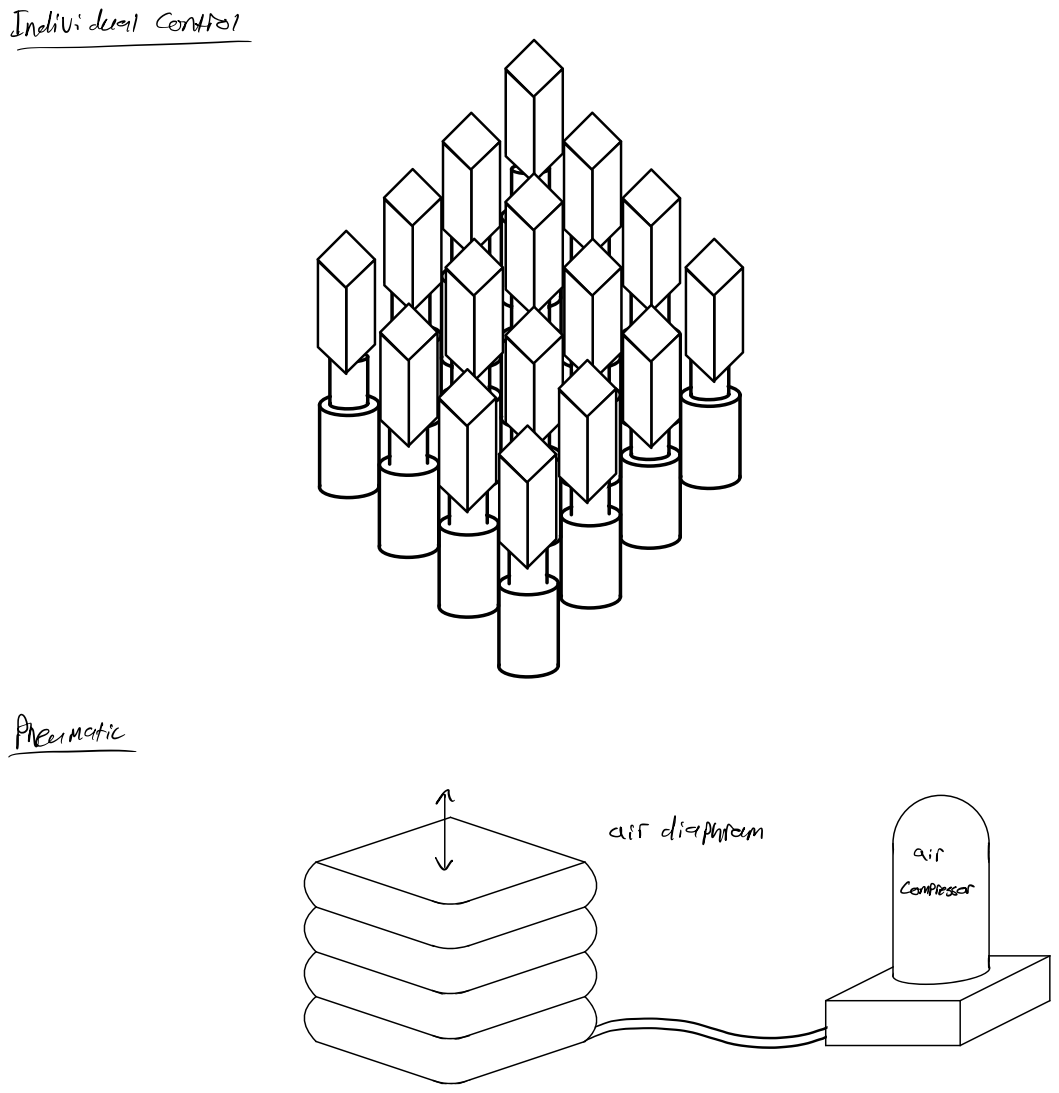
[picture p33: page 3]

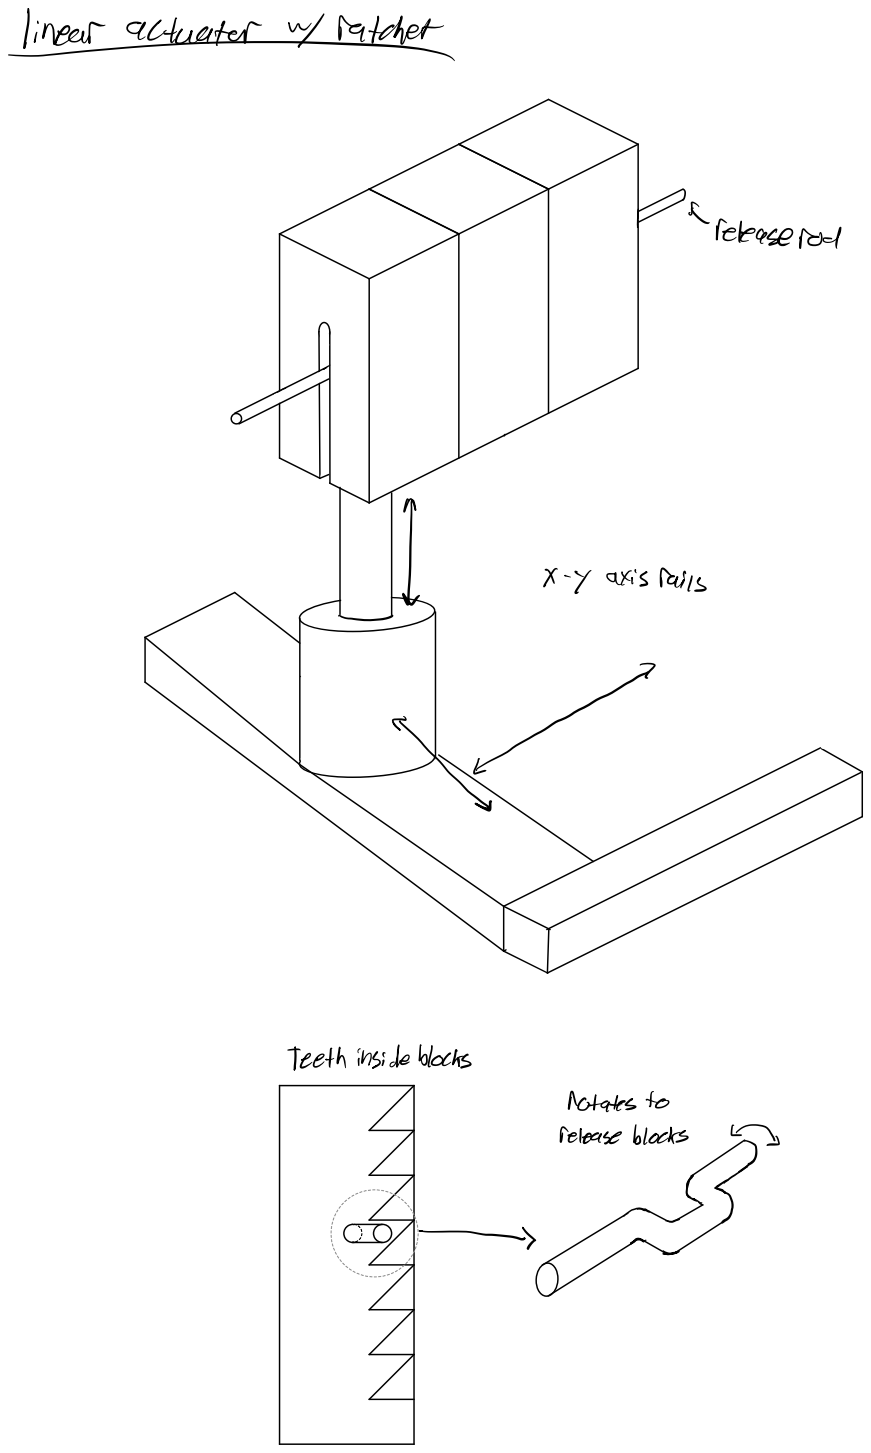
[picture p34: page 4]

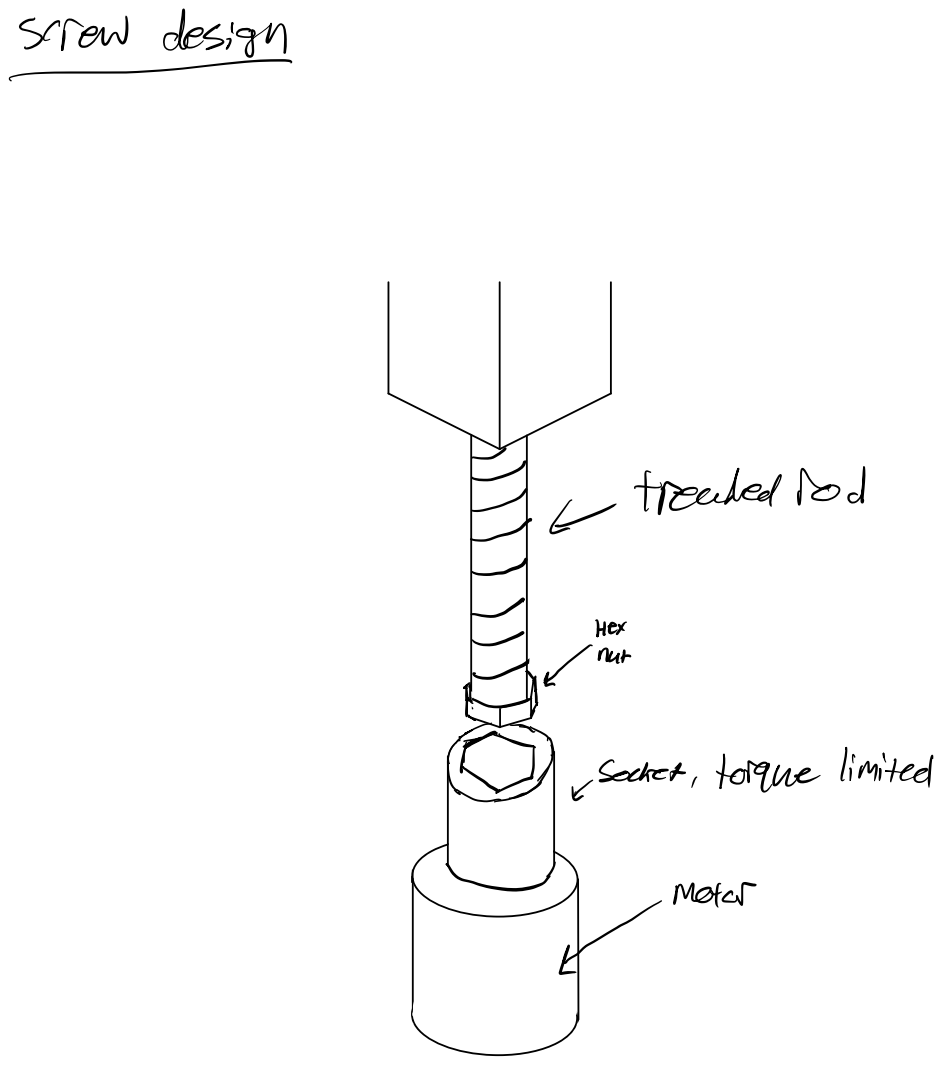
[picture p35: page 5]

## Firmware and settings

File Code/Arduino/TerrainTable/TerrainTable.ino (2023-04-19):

#include <ArduinoJson.h>

// Defines pins numbers
const int stepPin1 = 7;
const int stepPin2 = 8;
const int stepPin3 = 6;
const int stepPin4 = 9;
const int stepPin5 = 5;
const int stepPin6 = 10;
const int stepPin7 = 4;
const int stepPin8 = 11;
const int stepPin9 = 3;
const int stepPin10 = 12;
const int stepPinMasterSlave = 2;
const int stepPinRow = 12;

const int dirPin10 = 13; 
const int dirPin2 = 13; 
const int dirPin = 13; 


void setup() {
  // put your setup code here, to run once:
  pinMode(dirPin10,OUTPUT);
  pinMode(dirPin2,OUTPUT);
  pinMode(dirPin,OUTPUT);

  pinMode(stepPinRow,OUTPUT);
  pinMode(stepPinMasterSlave,OUTPUT);
  pinMode(stepPin1,OUTPUT);
  pinMode(stepPin2,OUTPUT);
  pinMode(stepPin3,OUTPUT);
  pinMode(stepPin4,OUTPUT);
  pinMode(stepPin5,OUTPUT);
  pinMode(stepPin6,OUTPUT);
  pinMode(stepPin7,OUTPUT);
  pinMode(stepPin8,OUTPUT);
  pinMode(stepPin9,OUTPUT);
  pinMode(stepPin10,OUTPUT);

  Serial.begin(9600);
}

void loop() {
  //Bring motors to row one - we can handle calibration of cubes in a separate sketch
  //Read for when the switch closes, stop the motor controlling row swap - now at row 1
  // 1. Bring motors up into cubes (.78 inches up into cubes) - 2 motors doing this
  // 2. Perform row 1 cube movements - 10 motors 
  // 3. Bring motors down from cubes (.78 inches down)
  // 4. Move forward 1 row (1 inch) - 1 motor
  // repeat steps 1 - 4 for all rows

  //Variable pins for now
  //while (!Serial.available()){} // wait for data to be available

  StaticJsonDocument<1024> doc; // adjust the size to match the serialized data
  //DeserializationError error = deserializeJson(doc, Serial);
  DeserializationError error = deserializeJson(doc, "[[3.0,3.0,3.0,3.0,3.0,3.0,3.0,3.0,3.0,3.0],[0.0,0.0,0.0,0.0,0.0,0.0,0.0,0.0,0.0,0.0],[0.0,0.0,0.0,0.0,0.0,0.0,0.0,0.0,0.0,0.0],[0.0,0.0,0.0,0.0,0.0,0.0,0.0,0.0,0.0,0.0],[0.0,0.0,0.0,0.0,0.0,0.0,0.0,0.0,0.0,0.0],[0.0,0.0,0.0,0.0,0.0,0.0,0.0,0.0,0.0,0.0],[0.0,0.0,0.0,0.0,0.0,0.0,0.0,0.0,0.0,0.0],[0.0,0.0,0.0,0.0,0.0,0.0,0.0,0.0,0.0,0.0],[0.0,0.0,0.0,0.0,0.0,0.0,0.0,0.0,0.0,0.0],[0.0,0.0,0.0,0.0,0.0,0.0,0.0,0.0,0.0,0.0]]");

  int grid[10][10];

  for (int row = 0; row < 10; row++) {
    for (int col = 0; col < 10; col++) {
      grid[row][col] = doc[row][col];
    }
  }

  //Set dirPin to HIGH
  digitalWrite(dirPin10, LOW);
  for (int gridRow = 0; gridRow < 10; gridRow++){

    //Raise motors to meet cube bracket
    digitalWrite(dirPin2, HIGH);
    for(int x = 0; x < 2800; x++){
      digitalWrite(stepPinMasterSlave, HIGH);
      digitalWrite(stepPinMasterSlave, LOW);
      delayMicroseconds(1500);
    }

    //Motor1 height = grid[gridRow][0];
    float h1 = grid[gridRow][0];
    h1 = (h1 / 100) * 3;
    int pulses1 = (h1 / 0.0654527559) * 1425;
    //Motor2 height2 = grid[gridRow][1];
    float h2 = grid[gridRow][1];
    h2 = (h2 / 100) * 3;
    int pulses2 = (h2 / 0.0654527559) * 1425;
    //Motor3 height3 = grid[gridRow][2];
    float h3 = grid[gridRow][2];
    h3 = (h3 / 100) * 3;
    int pulses3 = (h3 / 0.0654527559) * 1425;
    //Motor4 height4 = grid[gridRow][3];
    float h4 = grid[gridRow][3];
    h4 = (h4 / 100) * 3;
    int pulses4 = (h4 / 0.0654527559) * 1425;
    //Motor5 height5 = grid[gridRow][4];
    float h5 = grid[gridRow][4];
    h5 = (h5 / 100) * 3;
    int pulses5 = (h5 / 0.0654527559) * 1425;
    //Motor6 height6 = grid[gridRow][5];
    float h6 = grid[gridRow][5];
    h6 = (h6 / 100) * 3;
    int pulses6 = (h6 / 0.0654527559) * 1425;
    //Motor7 height7 = grid[gridRow][6];
    float h7 = grid[gridRow][6];
    h7 = (h7 / 100) * 3;
    int pulses7 = (h7 / 0.0654527559) * 1425;
    //Motor8 height8 = grid[gridRow][7];
    float h8 = grid[gridRow][7];
    h8 = (h8 / 100) * 3;
    int pulses8 = (h8 / 0.0654527559) * 1425;
    //Motor9 height9 = grid[gridRow][8];
    float h9 = grid[gridRow][8];
    h9 = (h9 / 100) * 3;
    int pulses9 = (h9 / 0.0654527559) * 1425;
    //Motor10 height10 = grid[gridRow][9];
    float h10 = grid[gridRow][9];
    h10 = (h10 / 100) * 3;
    int pulses10 = (h10 / 0.0654527559) * 1425;

    //Just putting the max possible height here for now
    for(int x = 0; x < 65315; x++) {
        delayMicroseconds(300); 
      if(x < pulses1){
        digitalWrite(stepPin1, HIGH);
        delayMicroseconds(300); 
        digitalWrite(stepPin1,LOW); 
        //delayMicroseconds(900); 
      }
      else{ delayMicroseconds(300); }

      if(x < pulses2){
        digitalWrite(stepPin2, HIGH);
        delayMicroseconds(300); 
        digitalWrite(stepPin2,LOW); 
        //delayMicroseconds(900); 
      }
      else{ delayMicroseconds(300); }

      if(x < pulses3){
        digitalWrite(stepPin3, HIGH);
        delayMicroseconds(300); 
        digitalWrite(stepPin3,LOW); 
        //delayMicroseconds(900); 
      }
      else{ delayMicroseconds(300); }

      if(x < pulses4){
        digitalWrite(stepPin4, HIGH);
        delayMicroseconds(300); 
        digitalWrite(stepPin4,LOW); 
        //delayMicroseconds(900); 
      }
      else{ delayMicroseconds(300); }

      if(x < pulses5){
        digitalWrite(stepPin5, HIGH);
        delayMicroseconds(300); 
        digitalWrite(stepPin5,LOW); 
        //delayMicroseconds(900); 
      }
      else{ delayMicroseconds(300); }

      if(x < pulses6){
        digitalWrite(stepPin6, HIGH);
        delayMicroseconds(300); 
        digitalWrite(stepPin6,LOW); 
        //delayMicroseconds(900); 
      }
      else{ delayMicroseconds(300); }

      if(x < pulses7){
        digitalWrite(stepPin7, HIGH);
        delayMicroseconds(300); 
        digitalWrite(stepPin7,LOW); 
        //delayMicroseconds(900); 
      }
      else{ delayMicroseconds(300); }

      if(x < pulses8){
        digitalWrite(stepPin8, HIGH);
        delayMicroseconds(300); 
        digitalWrite(stepPin8,LOW); 
        //delayMicroseconds(900); 
      }
      else{ delayMicroseconds(300); }

      if(x < pulses9){
        digitalWrite(stepPin9, HIGH);
        delayMicroseconds(300); 
        digitalWrite(stepPin9,LOW); 
        //delayMicroseconds(900); 
      }
      else{ delayMicroseconds(300); }

      if(x < pulses10){
        digitalWrite(stepPin10, HIGH);
        delayMicroseconds(300); 
        digitalWrite(stepPin10,LOW); 
        //delayMicroseconds(900); 
      }
      else{ delayMicroseconds(300); }

    
    //Lower motors to remove from cube bracket
    digitalWrite(dirPin2, LOW);
    for(int x = 0; x < 2800; x++){
      digitalWrite(stepPinMasterSlave, HIGH);
      digitalWrite(stepPinMasterSlave, LOW);
      delayMicroseconds(1500);
    }

    //Move forward a row unless on last row
    digitalWrite(dirPin, LOW);
    for(int x = 0; x < 130; x++){
      digitalWrite(stepPinRow, HIGH);
      digitalWrite(stepPinRow, LOW);
      delay(15);
    }
  }
}

}

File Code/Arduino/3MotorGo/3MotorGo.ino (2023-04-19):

#include <ArduinoJson.h>
#include <SD.h> // include the SD library

// Defines pins numbers
const int stepPin = 12;
const int dirPin = 13; 

int customDelay,customDelayMapped; // Defines variables
 
void setup() {
  // Sets the two pins as Outputs
  pinMode(stepPin,OUTPUT); 
  pinMode(dirPin,OUTPUT);
  pinMode(10,OUTPUT); 
  pinMode(9,OUTPUT);
  Serial.begin(9600);
}
void loop() {
    // while (!Serial.available()){
    //       Serial.print("Waiting");
    //       delay(1000);

    // } // wait for data to be available

//   StaticJsonDocument<1024> doc; // adjust the size to match the serialized data
//   DeserializationError error = deserializeJson(doc, Serial);
//   DeserializationError error = deserializeJson(doc, "[[1,2,3,4,5,6,7,8,9,10],[2,4,6,8,10,12,14,16,18,20],[3,6,9,12,15,18,21,24,27,30],[4,8,12,16,20,24,28,32,36,40],[5,10,15,20,25,30,35,40,45,50],[6,12,18,24,30,36,42,48,54,60],[7,14,21,28,35,42,49,56,63,70],[8,16,24,32,40,48,56,64,72,80],[9,18,27,36,45,54,63,72,81,90],[10,20,30,40,50,60,70,80,90,100]]");


//   if (error) {
//     Serial.print("Error parsing JSON: ");
//     Serial.println(error.c_str());
//     return;
//   }
//     int grid[10][10];

// for (int row = 0; row < 10; row++) {
//     for (int col = 0; col < 10; col++) {
//       grid[row][col] = doc[row][col];
//       String rowString = String(row);
//       String colString = String(col);
//       //Serial.print("Row " + rowString + " Column " + colString + " Value: ");
//       Serial.print("Row: ");
//       Serial.print(row);
//       Serial.print(" Column: ");
//       Serial.print(col);
//       Serial.print(" Value: ");
//       Serial.print(doc[row][col].as<int>());
//       Serial.print("\n");
//       delay(1000);
//     }
// }

///Calibration Code

///Run motors row by row

///Wait for clear 

//EVERY ROTATION IS 1.25 millimeters

  digitalWrite(dirPin,HIGH); // Enables the motor to move in a particular direction
  digitalWrite(10,HIGH);
  digitalWrite(9,HIGH);
  // Makes 200 pulses for making one full cycle rotation
  for(int x = 0; x < 1425; x++) {
    digitalWrite(stepPin,HIGH); 
    digitalWrite(10,HIGH);
    digitalWrite(9,HIGH);
    delayMicroseconds(1500); 
    digitalWrite(stepPin,LOW); 
    digitalWrite(10,LOW);
    digitalWrite(9,LOW);
    delayMicroseconds(1500); 
  }
  delay(500); // One second delay
  digitalWrite(dirPin,LOW); //Changes the rotations direction
  digitalWrite(10,LOW);
  digitalWrite(9,LOW);
  // Makes 400 pulses for making two full cycle rotation
  for(int x = 0; x < 1425; x++) {
    digitalWrite(stepPin,HIGH);
    digitalWrite(10,HIGH);
    digitalWrite(9,HIGH);
    delayMicroseconds(1500);
    digitalWrite(stepPin,LOW);
    digitalWrite(10,LOW);
    digitalWrite(9,LOW);
    delayMicroseconds(1500);
  }
  delay(500);
}

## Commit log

2023-04-18 Assessments and bill of materials
2023-04-19 Partial upload of 3D Files
    [Probe.prt, Probe.stl, Probe2.prt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]
